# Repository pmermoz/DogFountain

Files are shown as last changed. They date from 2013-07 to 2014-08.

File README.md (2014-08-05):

Dog Fountain
=========

The Garden's fountain for the dogs based on Arduino

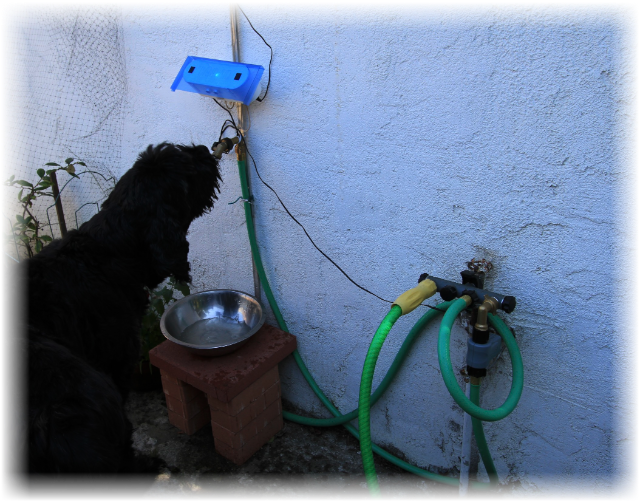
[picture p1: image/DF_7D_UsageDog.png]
Dog drinking


## Introduction

The project started with 2 dogs in a garden and bowls always empty or fill with dirty water. Dogs like fresh water, and two monsters of 100 lbs can consume a lot of water especially under the "hot" California climate.

The first approach was to use an "Outside Faucet Dog Waterer", a mechanical valve put on a faucet and activated by the dog tongue. One dog, the youngest one, try without consistent success and usually finished looking at me for help. The other didn’t even try to look at the valve.

I understand, with some training, both dogs can probably learn how to use a mechanical valve, just I found much more interesting to have a system more intuitive for the dog.

This experience shows:

- It’s not natural for a dog to go near a place where there is no water and push a "button" to get some.
- The youngest dog is always ready to try something new, but the oldest one has apparently some strict manners, and for him a dog should drink from a bowl, not from a faucet.
- When a dog sees water, or hears a water flow, and he is thirsty, he will come to see, and that is without training ;-)

At this point, the only solution was a robot to serve water to the dogs on demand ;-).

Some ideas:

- Start the water when dog approaches to get his attention.
- Avoid to stop the water when dogs are drinking (dog have a moderate sense of humor),
- Stop the water when the dog walks away (bill payer have a moderate sense of humor).
- Have a bowl placed under the faucet to respect “papa” dog habit,
- Try to not overfill the bowl, ideally balance the water output with the dog input.
- Try to have a simple design, simple to build.

## The result

It is now (as July 2014) for almost one year the fountain is online, the dogs use it every day.
I get 2 freezes of the fountain during the year, a simple power off/on solved the problem.

## Build Overview

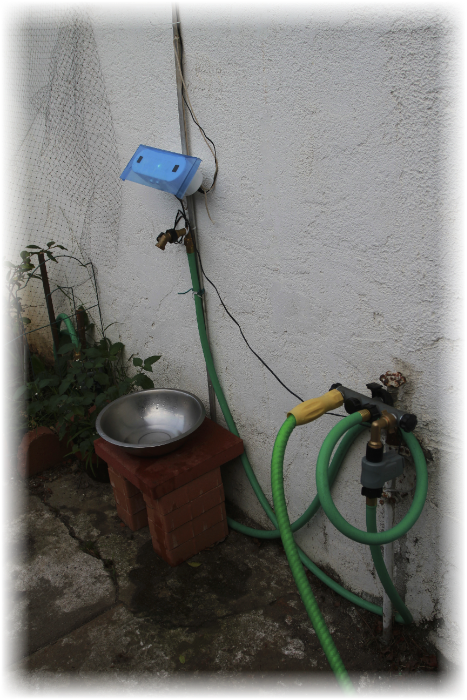
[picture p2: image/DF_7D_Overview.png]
Overview


The fountain is mainly composed of two parts:

* the brain, including CPU, sensors and relay
* the valve and faucet.

The existing wall faucet was too low for the dogs, and too cluttered by hoses. A garden hose is used to deport the fountain.

The fountain faucet is placed on the top of a bowl.

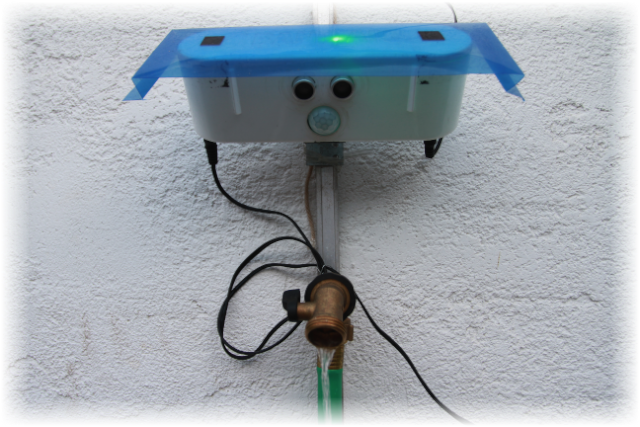
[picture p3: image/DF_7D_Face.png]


## Components

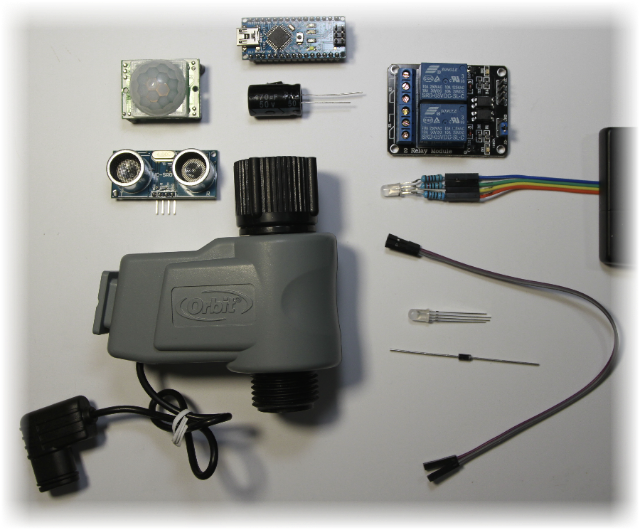
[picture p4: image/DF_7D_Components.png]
Components of the fountain


Components of the Garden's fountain for dogs 

## Water Valve

### Valve location choices

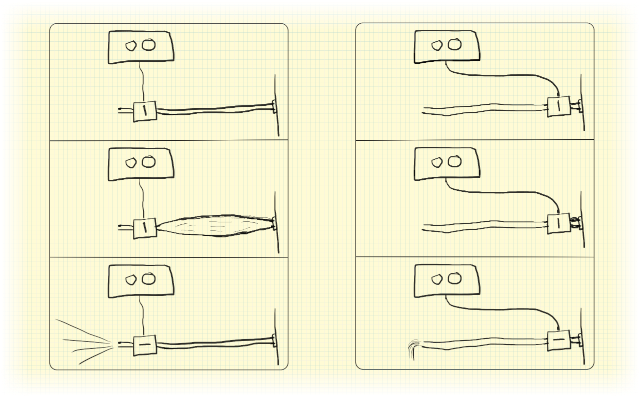
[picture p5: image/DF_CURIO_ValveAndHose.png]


Initially the valve was positioned at the extremity of the hose, but when the valve was closed, the water pressure was expanding the hose… and when the valve open, the elasticity of the hose added to the water pressure was generating a small jet of water...  
and dogs didn’t approve that.

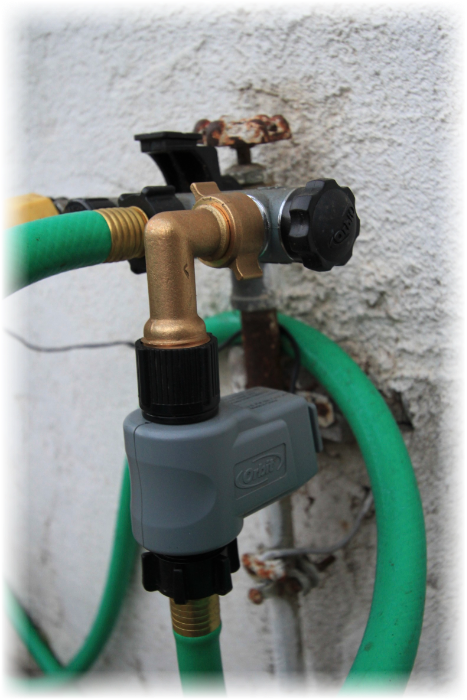
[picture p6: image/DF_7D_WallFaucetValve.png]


Moving the valve next to the wall faucet solved this inconvenience and we became friend again.

### Analyze of the valve

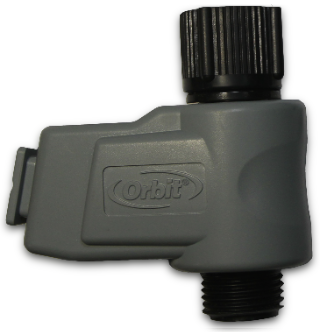
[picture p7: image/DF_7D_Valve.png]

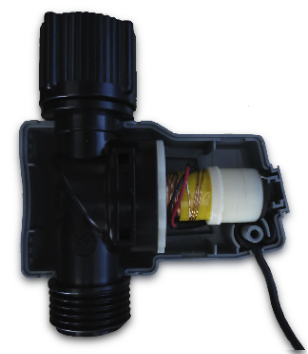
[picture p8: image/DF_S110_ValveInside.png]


I used one valve I had in stock, not too expensive and easy to find in store.

This valve is designed for battery powered controller, and gets two stable states.  
A DC current pulse is used to change the state between open and close.   
The polarity of the pulse defines the movement direction: open or close.

By testing this solenoid at various DC voltages, it appears that it could actuate down to 11V DC with a current of about 1.4A.
	
### Current and voltage at the valve when the valve open or close

Note:

* Yellow shows the voltage at the valve  
* Blue shows the current at the valve.

#### Valve open

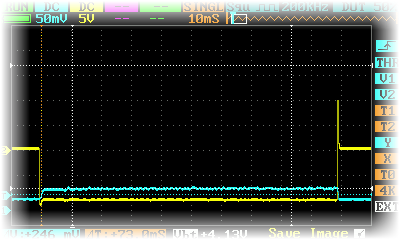
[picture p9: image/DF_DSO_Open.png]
  

Notice the pick of back-emf at the end.

If we zoom at the beginning of the pulse:

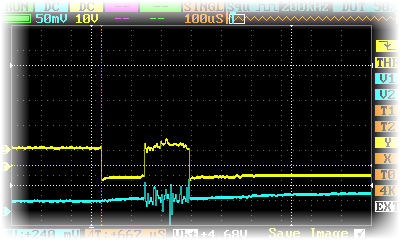
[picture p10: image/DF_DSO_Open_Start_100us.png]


we can see some fluctuation at the beginning, but nothing really bad.

On the other side, at the end of the pulse, we clearly see a back-emf effect when the current stop

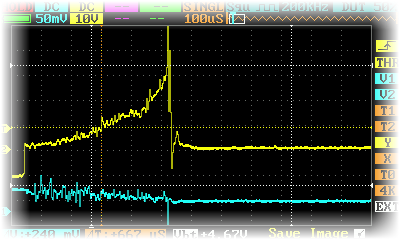
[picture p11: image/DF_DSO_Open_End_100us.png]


#### Valve Close
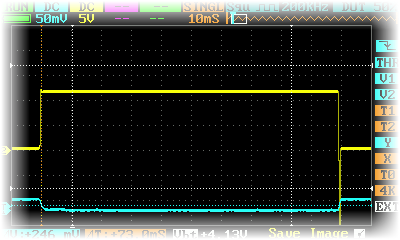
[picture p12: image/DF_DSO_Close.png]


### Timing

To estimate the pulse length needed to actuate, I recorded the valve sound and compared for different pulse length the variation of the sound envelop.

#### Valve Open
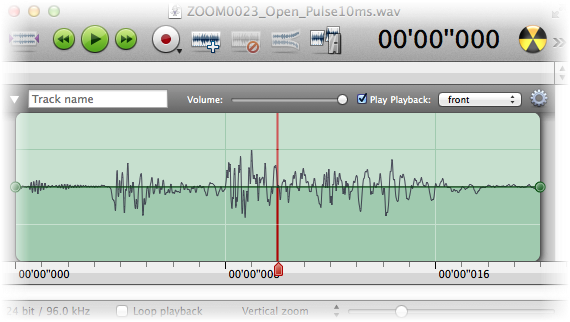
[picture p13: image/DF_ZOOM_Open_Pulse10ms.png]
   
10ms pulse

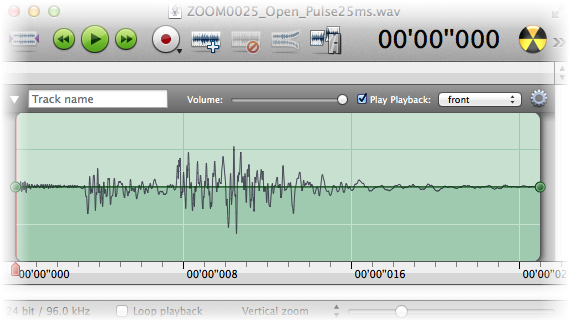
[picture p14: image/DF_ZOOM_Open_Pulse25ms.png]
   
25ms pulse

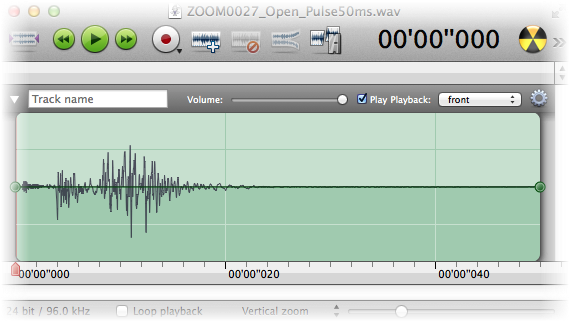
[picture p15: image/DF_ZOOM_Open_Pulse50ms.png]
   
50ms pulse

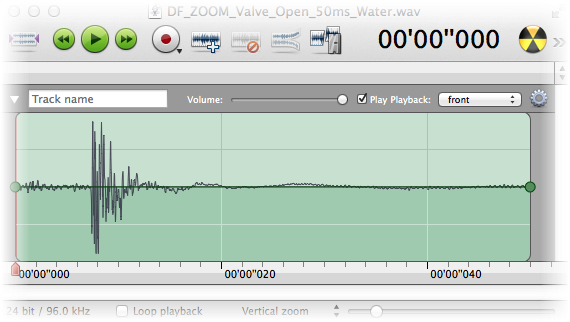
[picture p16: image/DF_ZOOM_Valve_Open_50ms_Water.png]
  
50ms pulse with water flow, without the relay noise. 

Analysis:
* 10ms pulse compared to the 25ms pulse shows missing power in the second part of the sound wave. 10ms is too short.
* On the other side 25ms compared to 50ms does not show any improvement.
* Presence of water flow does not seem to impact duration.

#### Valve Close
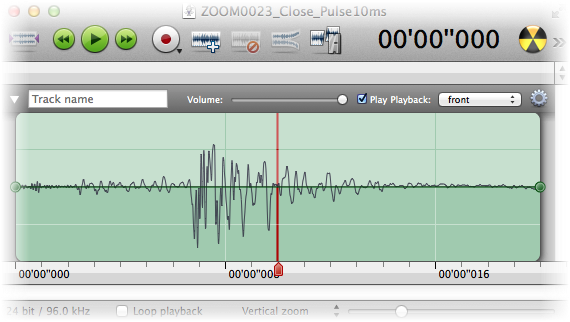
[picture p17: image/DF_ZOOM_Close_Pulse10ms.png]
  
10ms pulse

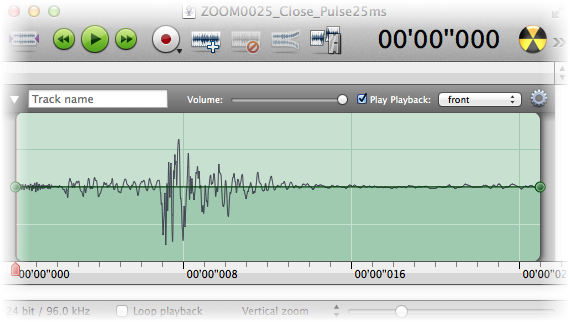
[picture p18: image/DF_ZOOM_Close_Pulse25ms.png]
  
25ms pulse

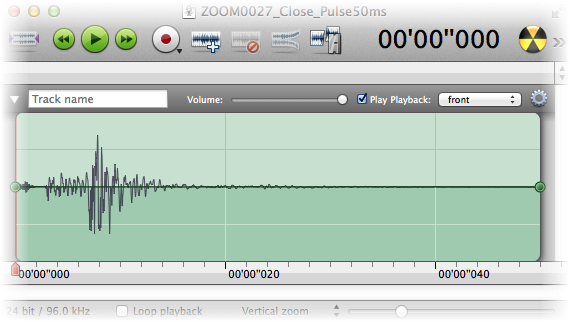
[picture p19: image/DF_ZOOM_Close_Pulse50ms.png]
  
50ms pulse

The close pulse does not show any difference starting at the 10ms pulse.

#### Detail of a 50ms pulse

Following captures show a 50ms pulse during the open and close.  
First, only the relay sound is recorded. In the order: relay 1 open, close, relay 2 open, and close.  
We can verify the time between the relay: open and close is timed to 50ms.

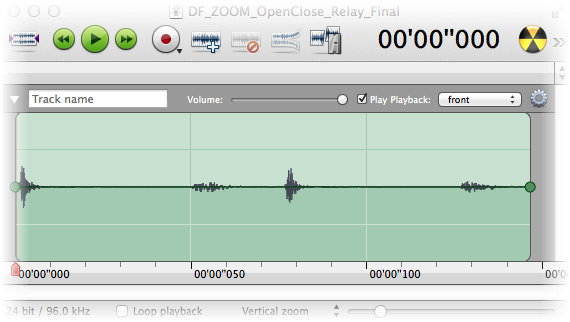
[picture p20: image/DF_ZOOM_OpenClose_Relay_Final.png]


Then, the relay and valve are recorded, with the same sequences.  
We can see much stronger noise created by the valve just after the relay actuates.  
We can also verify the margin between the pulse duration and the valve movement duration.

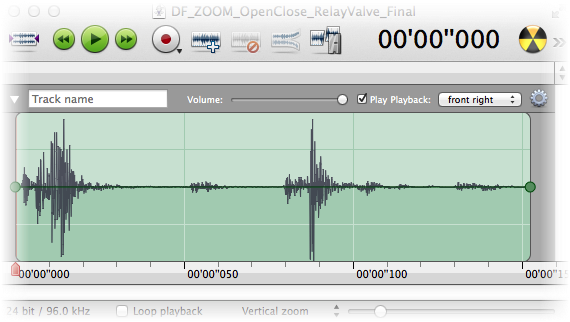
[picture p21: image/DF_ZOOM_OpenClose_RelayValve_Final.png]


#### Conclusion

A 20ms pulse should open the valve, and a 10ms pulse should close it.   
Closing the valve is an important step to avoid leak. Better to have a lot of margin here.   
To make it simple, we can set the pulse to 50ms in both directions.   
Open and closing of the valve does not happen often, valve is outside, solenoid temperature should not be a problem.

## Valve Connector

The Orbits valve gets a very small power cable, I needed a little more.  
The valve connects to a male connector not available in store, but creating one is pretty simple.

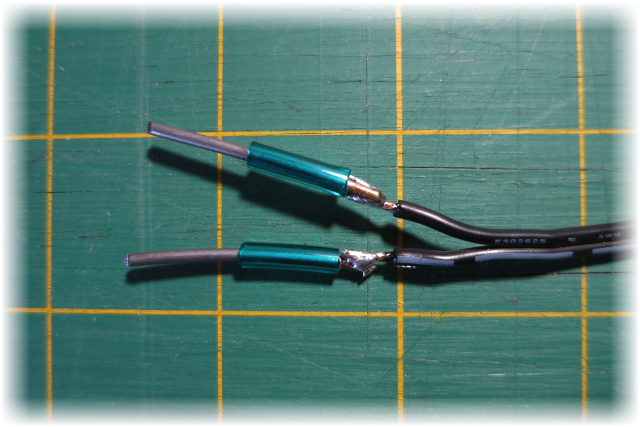
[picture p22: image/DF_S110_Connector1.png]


We use 1/16 (1.6mm) solid wire solder to a 2 wires extension cable.

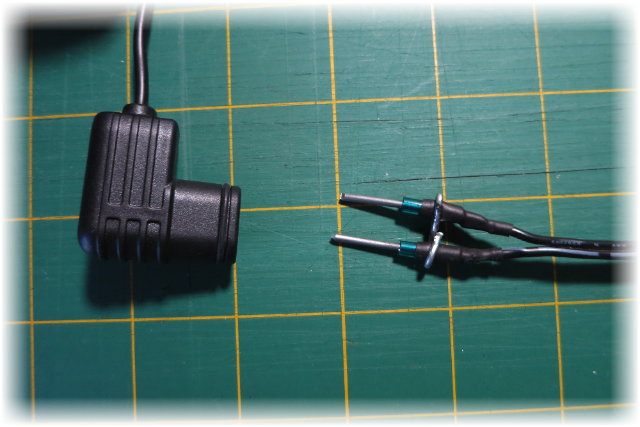
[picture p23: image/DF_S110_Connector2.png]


We add Heat-shrink tubing around the soldering, and use a smaller solid wire to keep the distance between the 2 solid wire pins.

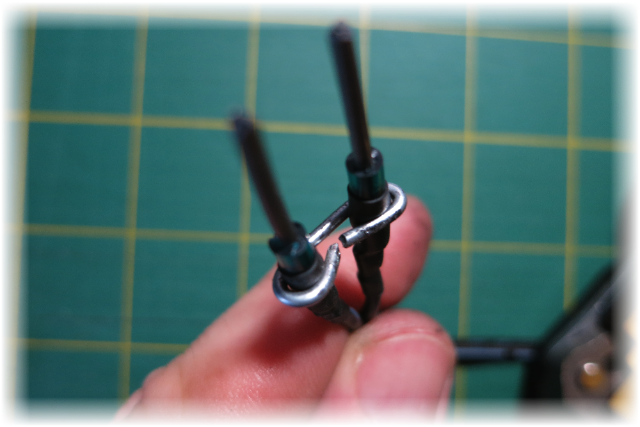
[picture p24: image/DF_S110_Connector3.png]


The smaller solid wire is turned around 2 pins providing a rigid assembly.

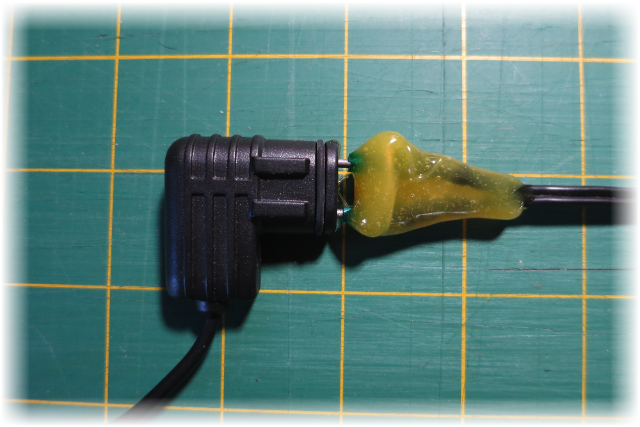
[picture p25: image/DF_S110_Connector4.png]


The pin space between the cable are filled with hot melt glue, using the transversal solid wire for support.

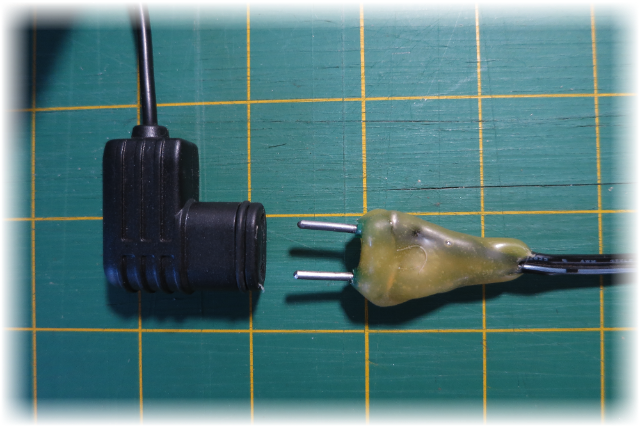
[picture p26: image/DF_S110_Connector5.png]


When cold, we cut the two pins to the correct lengths, and smoothing the extremities.
The white cable (positive) connects to the open pin of the Orbit connector.

Waterproofing needs to be added.

## Valve Relay

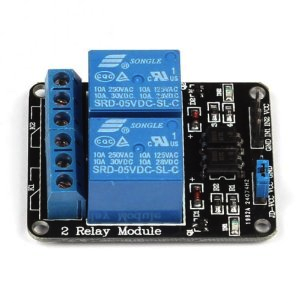
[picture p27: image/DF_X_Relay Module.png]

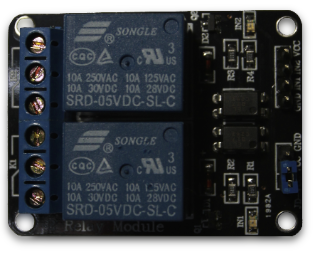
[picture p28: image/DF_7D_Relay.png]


The relays are used to commute the valve. It is a simple solution to commute 12V 1.5A.  
Each relay gets a contact normally-open and normally-close. Pulling to low IN1 or IN2 switch the relay.   
Two relays are needed to generate 3 states: Open Pulse, Close Pulse, and Stay.

### Valve Connection to Relay
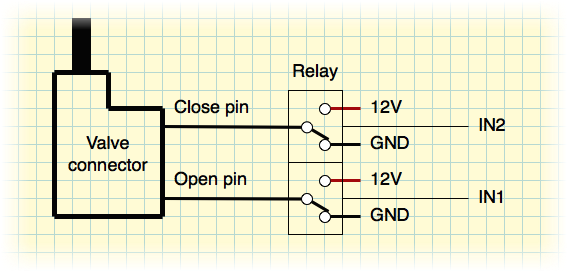
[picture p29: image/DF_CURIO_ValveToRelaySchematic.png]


The following table describes the action or the relay input on the valve:

 IN1	| IN2   | Open Pin | Close Pin | State | Description
--------|-------|----------|-----------|-------|----
 Low	| Low	| 12V		| 12V		| Stay | Keep valve state (not used)
 Low	|	High|	12V		| GND		| Open Pulse | Valve switch to Open
 High	|	Low	| GND		|	12V		| Close Pulse | Valve switch to close 
 High	| High	| GND		|	GND		| Stay  | Keep valve state

Reference:
* [wikipedia](http://en.wikipedia.org/wiki/Relay/)

## Fountain Sensor: Proximity

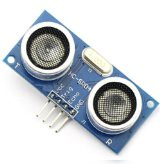
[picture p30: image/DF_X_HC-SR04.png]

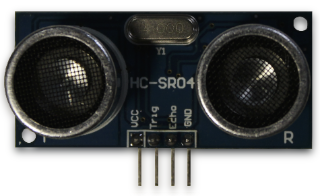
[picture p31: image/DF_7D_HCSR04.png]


The HC-SR04 Ultrasonic sensor is inexpensive and popular. It can determine the distance of an  object from 2cm (1”) to 3m (10ft) or more.  
The detection area is very narrow, about 2 degrees.

This sensor emits an ultrasonic sound (ping) and the time for the echo to come back gives the distance, like an active sonar.

This sensor gets few drawbacks:
* It is an active sensor, not sure how long before it will fail with continues operation.
* False positive if a fly is moving on the front of the sensor.
* Dog seems to hear the ultrasonic sound, and they might ignore if present continuously.

And some good sides:
* Dogs hear the ultrasonic sound, they can associate the sound with "Hey! Remember! Water is here!”.
* The sensor returns a distance, perfect to fine control of the valve activation.

Reference:
* [wikipedia](http://en.wikipedia.org/wiki/Sonar#Active_sonar)

## Fountain Sensor: PIR

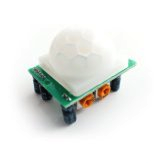
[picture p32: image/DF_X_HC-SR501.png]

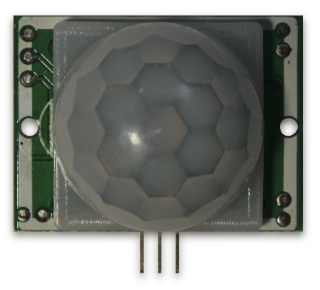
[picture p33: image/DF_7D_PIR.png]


PIR is also inexpensive and popular. It can sense motion of human or animal (heat source) up to 6m (20 ft).  
The detection area is wide, almost 180 degrees.

This sensor gets few drawback:
* It detects only movement of heat source, when the movement stops (dog drinking) the detection also stops.
* The PIR is sensitive to a lot of unwanted type of heat movement, like a flow of hot air, or the cloud that creates moving sun ray on the ground. Outside a PIR can generate a lot of false positive detection.
* Also the PIR gives a very basic information (movement detected) but lack details like the direction of the movement or if the dog is currently drinking, that will make difficult to optimize the water usage.

And some good sides:
* Passive, silence, and probably long life. Does not disturb the environment.
* Large detection area, can see the dog coming from far.

References:
* [wikipedia](http://en.wikipedia.org/wiki/Passive_infrared_sensor)
* [ladyada](http://www.ladyada.net/learn/sensors/pir.html)

## Sensors usage

The idea is to use a tandem of two sensors to detect dog presence and trigger the water flow.

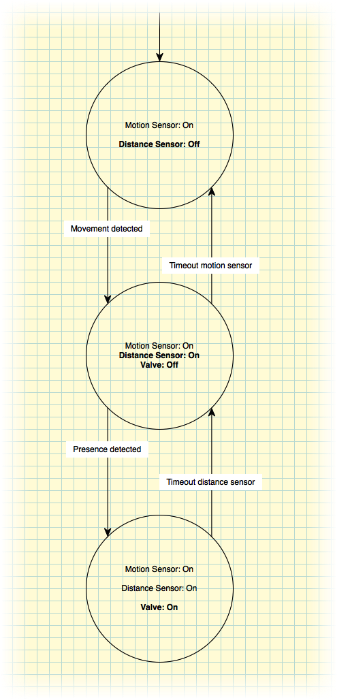
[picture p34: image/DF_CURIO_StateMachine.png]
State


Using a combination of both sensor can improve the detection:
- Initially the ultrasonic sensor is turned off.
- The PIR sensor “scans” the region around the fountain.
- When a dog approaches, the PIR detects the movement and the Ultrasonic sensor starts.
- When the dog reaches the fountain, the Ultrasonic sensor triggers the water fountain
- When the dog leaves, the Ultrasonic sensor triggers the fountain stop
- After a while, if no more movement, the PIR stops the Ultrasonic sensor.  

## Feedback: RGB LED



The LED is very useful to debug the fountain code.  
At night the box is glowing with a pulsing white light when the fountain sleeps... very nice effect.

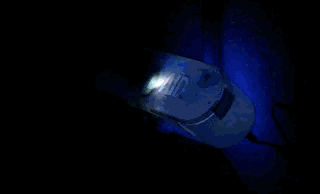
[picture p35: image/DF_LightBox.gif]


The RGB led provides the following feedback (in order):

Light	| Description
--------|----------
Green | Near presence detected (ultrasonic)
Yellow (Red+Green) | Far presence detected (ultrasonic debug)
Red	| Motion detected (PIR)
Blue | PIR was recently triggered, but no more
White pulsing | Fountain is sleeping
Black | Do you have power?

Note: 
* The table order indicates what will be the feedback if multiple sensors are trigged at the same time, for example if we have both the PIR and ultrasonic, then we will get only the Ultrasonic indication.
* The white pulsing appears if nothing else is present.

The Arduino Nano can provide up to 40mA for each pin. 

We do not need the usual 20mA per LED, 9mA should be enough for our usage.
From the measure of the forward voltage for each color, we get the value for each resistor

Color | FV | ohm
------|---:|----:
Red   |1.7V|180
Green |2.4V|100
Blue  |2.5V|100

## CPU

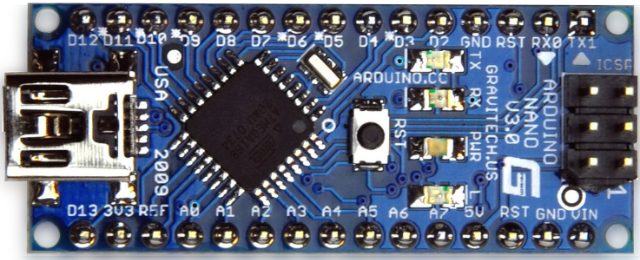
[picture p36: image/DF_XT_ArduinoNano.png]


The fountain is based on an Arduino nano, small and inexpensive.

References: 
* [Arduino](http://arduino.cc)

## Fountain Body

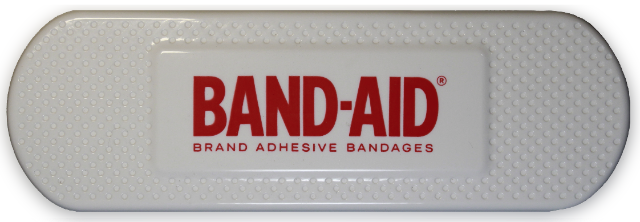
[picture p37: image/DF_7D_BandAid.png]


The COSTCO Band-aid box fits very nicely for the purpose.  
The good size, and the compartments inside fit the Arduino and relay almost perfectly. 

## Power Supply

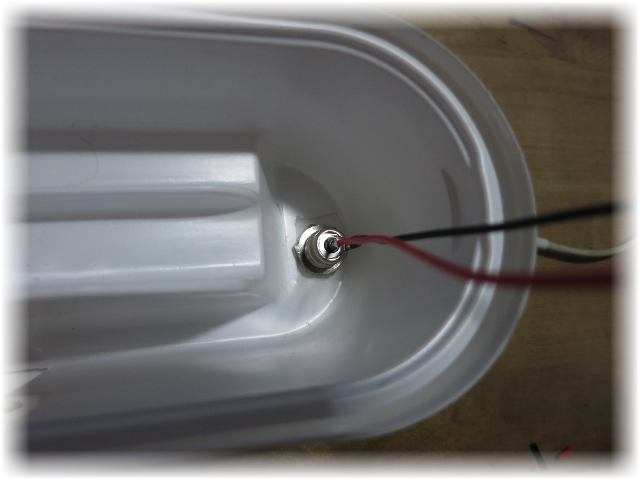
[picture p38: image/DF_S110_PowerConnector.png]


A standard power supply is used, and a connector is added to the bottom of the box.

Note: The same connector is used to connect to the valve.

## Schematic

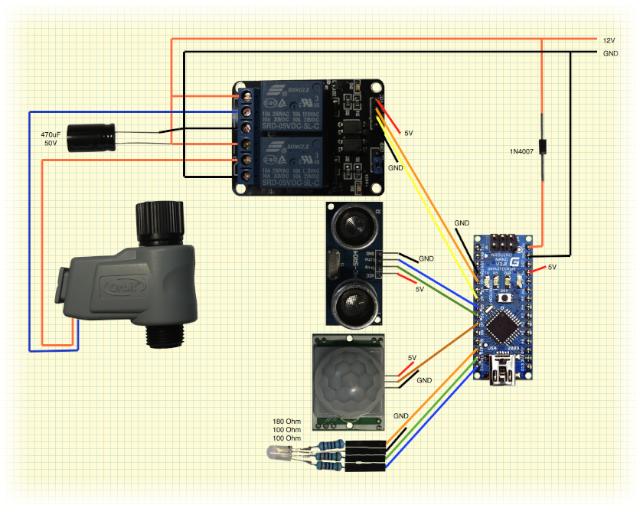
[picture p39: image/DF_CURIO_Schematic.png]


The schema is pretty simple, few soldering are needed.  

A capacitor (470µF) was added to the power line energizing the valve.  
The capacitor provides a reserve of energy for the valve, and removes all visible back-emf to the power line.  
Without the capacitor, the Arduino is completely unstable.

Note: the capacitor cannot be place directly on the valve because of the valve inversion of polarity.  

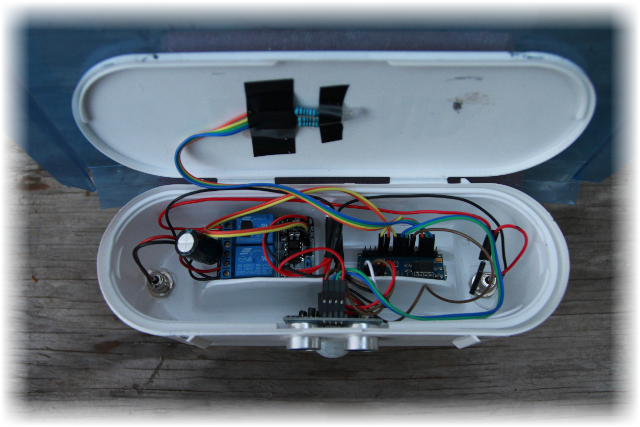
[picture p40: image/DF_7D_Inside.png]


Most connections use Female to Female jumper cable.

The “hat” is a cut from a plastic envelope, fixed on the top of a Band-Aid box.  
That was nice looking hat... but after a year the plastic didn't survive the sun :(

## Parts and Cost

Description | Reference | Quantity | Price | Store
------------|-----------|---------:|------:|:-----:
CPU | Arduino Nano v3.0 | 1 | $13.99 | [Amazon](http://www.amazon.com/SainSmart-Nano-v3-0-for-Arduino/dp/B00761NDHI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)
Valve| Orbit extra valve | 1 | $13.56 | [Amazon](http://www.amazon.com/Orbit-58874N-Extra-Complete-Watering/dp/B003LY4I2I/ref=pd_sim_lg_2)
Sensor | 2-Channel Relay Module | 1 | $7.18 | [Amazon](http://www.amazon.com/SainSmart-2-CH-2-Channel-Relay-Module/dp/B0057OC6D8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)
Power Supply | DC 12V 1.5A | 1 | $7.00 |
Connector| 2.1mmx5.5mm DC Power Jack Socket Female | 2 | $5.32 | [Amazon](http://www.amazon.com/gp/product/B00JR591DG/ref=ox_sc_act_title_1?ie=UTF8&psc=1&smid=A1THAZDOWP300U)
Sensor | HC-SR04 Ultrasonic Distance Sensor | 1 | $3.13 | [Amazon](http://www.amazon.com/SainSmart-HC-SR04-Ranging-Detector-Distance/dp/B004U8TOE6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)
Sensor | HC-SR501 Human Sensor Module Pyroelectric Infrared | 1 | $2.67 | [Amazon](http://www.amazon.com/HC-SR501-Sensor-Module-Pyroelectric-Infrared/dp/B007XQRKD4/ref=pd_bxgy_e_text_y)
Component| Resistors: 1x 180 ohm, 2x 100 ohm| 3 | $0.10 |
Component| RGB Led ($2.67/50)| 1 | $0.05 | [Amazon](http://www.amazon.com/gp/product/B005VMDROS)
Component| Capacitor | 1 | $0.03 | [Amazon](http://www.amazon.com/Joe-Knows-Electronics-Value-Capacitor/dp/B007SVHFXO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)
Cable | 20cm Female to Female 2.54mm 0.1 Inch Jumper Cable Wires Connector ($3.99/5)| 1 | $0.80 | [Amazon](http://www.amazon.com/gp/product/B00D8WOWMY)
Box| COSTCO’s Band-Aid (Recycling) | 1 | $0.00 | COSTCO
***Total*** | | | ***$53.83*** |

<!--| DC Power connector 2.1mm x 5.5mm Female | 2 | $7.00 | [Radioshack](http://www.radioshack.com/product/index.jsp?productId=2102486)-->

## Prototype & Test



Testing the PIR and Ultrasonic distance sensor.



First prototype and it's beautiful box  :)  
Notice the relay directly connected to the wall faucet.



Test of all components before integration.



Testing a configuration of the fountain faucet. The valve and the "jet" effect.

#### Testing of the valve



A simple setup to test the valve. The valve is controlled by 2 switches.

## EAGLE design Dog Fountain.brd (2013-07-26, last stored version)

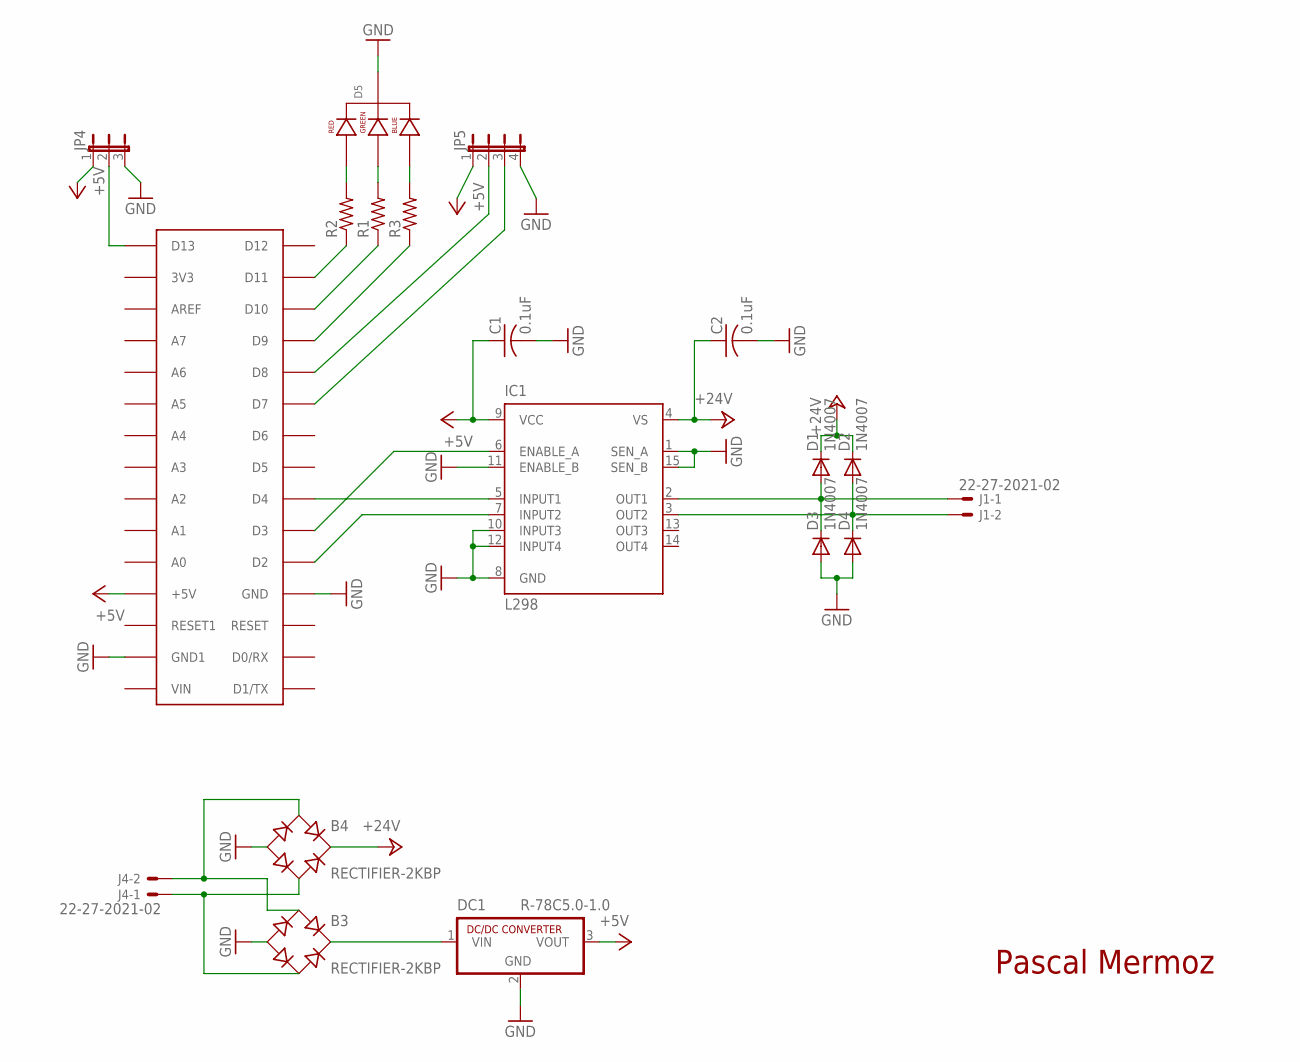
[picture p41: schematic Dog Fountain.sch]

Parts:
B3, B4: RECTIFIER-2KBP; 2KBP; MPN KBP202G
C1, C2: 0.1uF; C050-024X044; MPN C317C104K5R5TA
D1, D2, D3, D4: 1N4007; DO41-10; MPN KBP202G
D5: LED-RGB-CC-THRUDIFFUSE; LED-RGB-THRU
DC1: R-78C5.0-1.0; SIP3; MPN OKI-78SR-5/1.5-W36-C
IC1: L298; MULTIWATT-15
J1, J4: 22-27-2021-02; 6410-02
JP4: JP2E; JP2
JP5: JP4E; JP4
R1, R2, R3: R-US_0204/2V; 0204V
U$1: ARDUINONANO; PDIP-32; MPN A000005

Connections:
+5V: C1.1, DC1.3 (VOUT), IC1.9 (VCC), JP4.1, JP5.1, U$1.+5V
+24V: B4.+, C2.1, D1.C, D2.C, IC1.4 (VS)
GND: B3.-, B4.-, C1.2, C2.2, D3.A, D4.A, D5.2 (CATHODE), DC1.2 (GND), IC1.1 (SEN_A), IC1.8 (GND), IC1.10 (INPUT3), IC1.11 (ENABLE_B), IC1.12 (INPUT4), IC1.15 (SEN_B), JP4.3, JP5.4, U$1.GND, U$1.GND1
unnamed: B3.+, DC1.1 (VIN)
unnamed: IC1.6 (ENABLE_A), U$1.D3
unnamed: IC1.5 (INPUT1), U$1.D4
unnamed: D2.A, D4.C, IC1.3 (OUT2), J1.2
unnamed: D1.A, D3.C, IC1.2 (OUT1), J1.1
unnamed: IC1.7 (INPUT2), U$1.D2
unnamed: B3.AC1, B4.AC1, J4.2
unnamed: B3.AC2, B4.AC2, J4.1
unnamed: JP4.2, U$1.D13
unnamed: JP5.2, U$1.D8
unnamed: JP5.3, U$1.D7
unnamed: R3.1, U$1.D9
unnamed: R1.1, U$1.D10
unnamed: R2.1, U$1.D11
unnamed: D5.1 (RED_CATHODE), R2.2
unnamed: D5.3 (GREEN_CATHODE), R1.2
unnamed: D5.4 (BLUE_CATHODE), R3.2

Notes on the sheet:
Pascal Mermoz

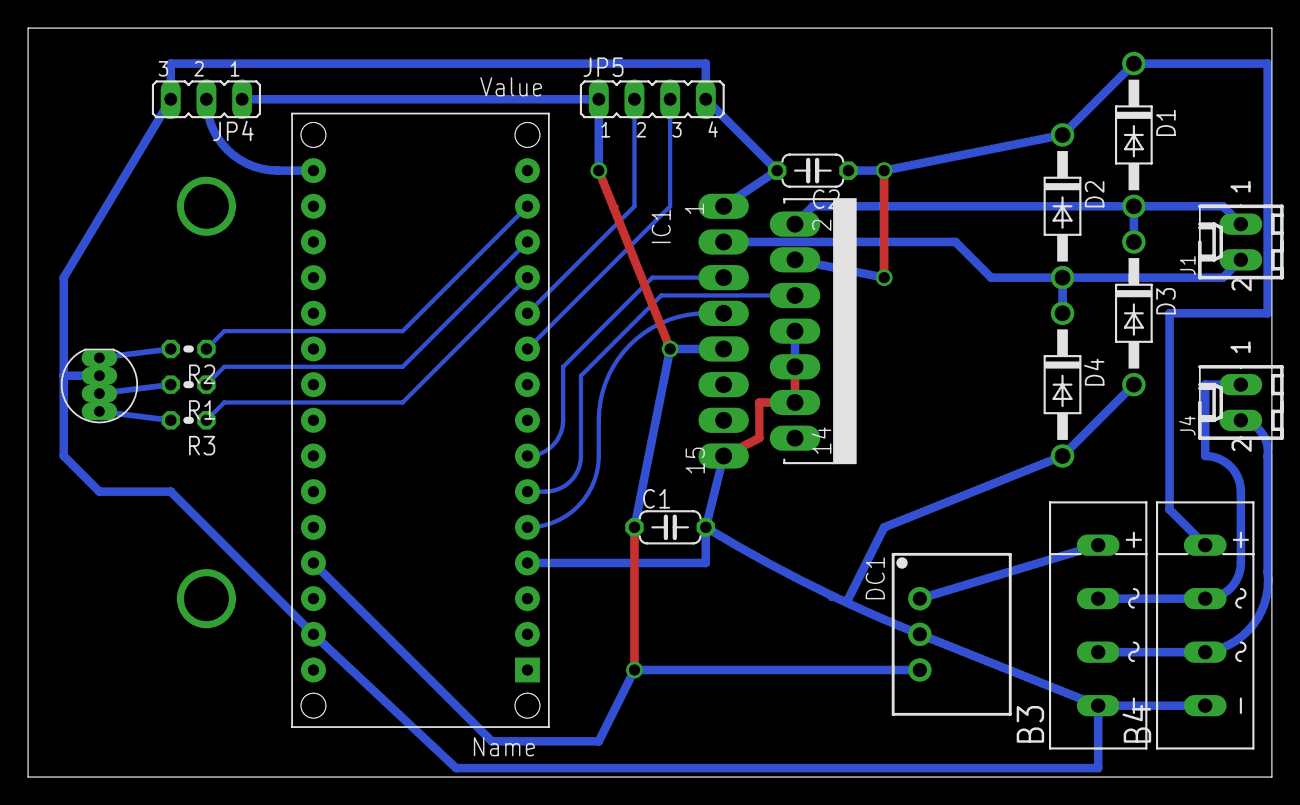
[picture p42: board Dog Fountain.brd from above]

Board: 2 copper layers, 88.6 x 53.3 mm, 19 parts (0 on the bottom side), 20 nets.

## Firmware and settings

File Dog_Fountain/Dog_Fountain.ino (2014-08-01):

#include <NewPing.h>

//--- PIR
const int PIR_INPUT = 7;
const long PIR_DETECTION_DURATION = 5 * 1000;

//--- Sonar (HC-SR04)
const int HC_SR04_ECHO_PIN = 5;
const int HC_SR04_TRIGGER_PIN = 6;

const int LED_RED_DISTANCE_PIN = 9;
const int LED_GREEN_DISTANCE_PIN = 10;
const int LED_BLUE_DISTANCE_PIN = 11;

const long PING_EVERY = 500;
const long PING_FEEDBACK_DURATION = 200;
const long SONAR_DETECTION_DURATION = 5000;
const int SONAR_DETECTION_DISTANCE = 60;
const int SONAR_MAX_DISTANCE = SONAR_DETECTION_DISTANCE + (SONAR_DETECTION_DISTANCE / 5) ; // Maximum distance we want to ping for (in centimeters). Maximum sensor distance is rated at 400-500cm.

//--- Valve
const int VALVE_1_ON_PIN = 4;
const int VALVE_1_OFF_PIN = 2;
const int SWITCH_DELAY_MS = 50;

const long MIN_WATERING_DURATION = 5 * 1000;


NewPing sonar(HC_SR04_TRIGGER_PIN, HC_SR04_ECHO_PIN, SONAR_MAX_DISTANCE); // NewPing setup of pins and maximum distance.

unsigned long pirDetectionUntilTimeMs;
unsigned long sonarDetectionUntilTimeMs;
unsigned long wateringUntilTimeMs;

unsigned long nextPingTimeMs;

boolean didDetectPresence = false;
boolean didDetectFarePresence = false;

long distanceCm = 0;

boolean isWatering = false;

//---

void setup()
{
  //--- PIR

  pinMode(PIR_INPUT, INPUT);

  //--- Sonar

  pinMode(HC_SR04_TRIGGER_PIN, OUTPUT);
  pinMode(HC_SR04_ECHO_PIN, INPUT);
  pinMode(LED_RED_DISTANCE_PIN, OUTPUT);
  pinMode(LED_GREEN_DISTANCE_PIN, OUTPUT);
  pinMode(LED_BLUE_DISTANCE_PIN, OUTPUT);

  nextPingTimeMs = 0;

  //--- Valve

  pinMode(VALVE_1_ON_PIN, OUTPUT);
  pinMode(VALVE_1_OFF_PIN, OUTPUT);
  digitalWrite(VALVE_1_ON_PIN, HIGH);
  digitalWrite(VALVE_1_OFF_PIN, HIGH);

  valveOff();
}

void loop()
{ 
  unsigned long nowTimeMs = millis();

  //--- PIR

  boolean didPIRDetect = digitalRead(PIR_INPUT);
  if (didPIRDetect) {
    // PIR detection is valid until pirDetectionUntilTimeMs
    pirDetectionUntilTimeMs = nowTimeMs + PIR_DETECTION_DURATION;
  }

  //--- Sonar

  // To start Sonar ping we need PIR detection (to limit usage of sonar and reduce sonar life)
  // Sonar successfull detection will start watering
  // Keep Sonar while PIR or Sonar recently get detection
  // No Sonar detection for a while will trigger stop watering (after water timeout)
  // Watering have a minimal duration (timeout) to avoid rapid pulse of water (not good for relay... and dog)
  if (pirDetectionUntilTimeMs > nowTimeMs || sonarDetectionUntilTimeMs > nowTimeMs) {
    if (nowTimeMs > nextPingTimeMs) {
      // Wait 500ms between pings (about 2 pings/sec). 29ms should be the shortest delay between pings.
      nextPingTimeMs = nowTimeMs + PING_EVERY;

      didDetectPresence = false;
      didDetectFarePresence = false;

      //long echoTime = sonar.ping_median(3); // Send ping, get ping time in microseconds (uS).
      long echoTime = sonar.ping(); // Send ping, get ping time in microseconds (uS).
      distanceCm = sonar.convert_cm(echoTime);

      if (distanceCm > 0) {
        if (distanceCm < SONAR_DETECTION_DISTANCE) {
          didDetectPresence = true;

          // Sonar detection is valid until sonarDetectionUntilTimeMs
          sonarDetectionUntilTimeMs  = nowTimeMs + SONAR_DETECTION_DURATION;

          if (!isWatering) {
            valveOn();
            wateringUntilTimeMs = nowTimeMs + MIN_WATERING_DURATION;
          }
        }
        else {
          didDetectFarePresence = true;
        }
      }
      if (isWatering && nowTimeMs > sonarDetectionUntilTimeMs && nowTimeMs > wateringUntilTimeMs) {
        valveOff();
      }
    }
    // No else, we do not stop water between ping...
  }
  else {
    didDetectPresence = false;
    didDetectFarePresence = false;
    if (isWatering && nowTimeMs > wateringUntilTimeMs) {
      valveOff();
    }
  }

  //--- Feedback
  
  // Pulsing white    Sleep
  // RED              PIR detection
  // BLUE             PIR was detected
  // Light GREEN      Fare presence detected
  // GREEN            Presence detected during last SONAR_DETECTION_DURATION

  if (pirDetectionUntilTimeMs < nowTimeMs && sonarDetectionUntilTimeMs < nowTimeMs) {
    // Nothing
    int pulsePeriod = 6 * 1000;
    int pulseHalfPeriod = pulsePeriod / 2;
    int feedbackStep = (nowTimeMs % pulsePeriod);
    int lightLevel;
    if (feedbackStep < pulseHalfPeriod) {
      lightLevel = map(feedbackStep, 0, pulseHalfPeriod, 0, 127);
    }
    else {
      lightLevel = map(feedbackStep, pulseHalfPeriod, pulsePeriod, 127, 0);
    }

    analogWrite(LED_RED_DISTANCE_PIN, lightLevel);
    analogWrite(LED_GREEN_DISTANCE_PIN, lightLevel);
    analogWrite(LED_BLUE_DISTANCE_PIN, lightLevel);
  }
  else if (didDetectPresence) {
    digitalWrite(LED_RED_DISTANCE_PIN, LOW);
    digitalWrite(LED_GREEN_DISTANCE_PIN, HIGH);
    digitalWrite(LED_BLUE_DISTANCE_PIN, LOW);
  }
  else if (didDetectFarePresence) {
    digitalWrite(LED_RED_DISTANCE_PIN, HIGH);
    digitalWrite(LED_GREEN_DISTANCE_PIN, HIGH);
    digitalWrite(LED_BLUE_DISTANCE_PIN, LOW); 
  }
  else if (didPIRDetect) {
    digitalWrite(LED_RED_DISTANCE_PIN, HIGH);
    digitalWrite(LED_GREEN_DISTANCE_PIN, LOW);
    digitalWrite(LED_BLUE_DISTANCE_PIN, LOW);
  }
  else if (pirDetectionUntilTimeMs >  nowTimeMs) {
    digitalWrite(LED_RED_DISTANCE_PIN, LOW);
    digitalWrite(LED_GREEN_DISTANCE_PIN, LOW);
    digitalWrite(LED_BLUE_DISTANCE_PIN, HIGH);
  }
  else
  {
    digitalWrite(LED_RED_DISTANCE_PIN, LOW);
    digitalWrite(LED_GREEN_DISTANCE_PIN, LOW);
    digitalWrite(LED_BLUE_DISTANCE_PIN, LOW);
  }
}

void valveOn() {
  digitalWrite(VALVE_1_OFF_PIN, HIGH);
  digitalWrite(VALVE_1_ON_PIN, LOW);
  delay(SWITCH_DELAY_MS);
  digitalWrite(VALVE_1_ON_PIN, HIGH);

  isWatering = true;
}

void valveOff() {
  digitalWrite(VALVE_1_ON_PIN, HIGH);
  digitalWrite(VALVE_1_OFF_PIN, LOW);
  delay(SWITCH_DELAY_MS);
  digitalWrite(VALVE_1_OFF_PIN, HIGH);

  isWatering = false;
}

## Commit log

2013-07-26 Initial checkin
    [Dog Fountain.brd, Dog Fountain.sch]
2013-08-03 PCB board first test
    [Dog Fountain.brd, Dog Fountain.sch]
2013-08-03 - Change AnalogWrite to DigitalWrite (no PWM on Analog pin) - Fix pin assignment
    [Dog_Fountain.ino]
2013-08-10 Another try with 12v power supply
    [Dog Fountain.brd, Dog Fountain.sch]
2013-08-18 Drop PCB board, use 12v power supply, relay, and Dupont connector. Get a pulse white light, change detection logic.
2013-10-15 - Sonar detection extended from 2.5s to 5s - Sleep pulse light extends from 5s to 6s period
2014-02-03 - cleanup - documentation (WIP)
    [Dog Fountain.brd, Dog Fountain.sch, Dog_Fountain_1_2.brd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]

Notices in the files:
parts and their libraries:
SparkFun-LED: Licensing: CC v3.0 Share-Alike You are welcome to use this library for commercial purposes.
